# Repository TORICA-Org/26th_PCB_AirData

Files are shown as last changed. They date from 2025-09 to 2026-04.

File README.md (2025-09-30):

# 26th_PCB_AirData
メイン兼エアデータセンサー部（今後，エアデータと言います）のリポジトリです．
## 基板作成時の注意点
PCBエディターで基板上の配線をするときに気をつけてほしい点・できるだけ避けるべき点が書いてあります．これが全てではないのですが，最低限これらは守ってほしいです🙏( ｀・∀・´)ﾉﾖﾛｼｸ  
また，基板作成のコツを最後に載せてあります  
### KiCadの初期設定
これから表面実装化に向けた，小さく密度の高い基板を作ろうとするとKiCadの初期設定状態では不便が生じます．それは例えば配線のクリアランス（配線同士の最低間隔）やビア半径の初期設定値が大きすぎるためです．  
以下の画像下部のGNDビアはその上のコンデンサと同じぐらいの大きさになっていて，もはや邪魔です．  
  
そこで，以下の画像左上「ビア：ネットクラスのサイズを使用」からより小さい半径を指定できるのですが，[JLCPCBの製造能力](https://jlcpcb.com/jp/capabilities/pcb-capabilities)には限界があるわけでその限界を突破しないギリギリで設計する必要があります．その限界を突破していないか確認してくれる機能を活用するためにKiCad初期設定を変更します．この設定はプロジェクトを新たに作成する際に毎回設定する必要があります．  
  
ただし注意点の一つとして，**ビアのサイズを小さくすると急激に価格が跳ね上がる**ということがあります．これはJLCPCBの製造能力ページを見るだけではわからず，発注画面まで行って分かることなのですがビア外径0.4mm，内径0.3mmを下回るサイズのビアを打つとその個数に関わらず＋￥7200~9700されます．絶望ですね．はい...気をつけましょう．私はそんなことも知らず発注直前まで行って気付き，1430個のビアを打ち直すことになりました(┬┬﹏┬┬)
  
1. ファイル ＞ 基板の設定
  

2. デザインルール ＞ 制約


3. 以下のようにパラメータを変更  
  

---  

### USBの配線について
USBは差動伝送で通信しています．そのため，2本の配線のどちらかにだけノイズが乗ることや配線長に差があること，配線が長すぎることは避けるべきです．また，差動インピーダンスを考慮する必要があり，普段の配線よりも気を使う点が多いです．以下の点に気をつけて配線をお願いします．  
- 差動インピーダンスを90Ωに近づける（[JLCPCB公式計算ツール](https://jlcpcb.com/jp/pcb-impedance-calculator)）
- KiCad「配線 ＞ 差動ペアの配線」機能を使用する  
スクリーンショット (257)

- 同一レイヤー上で配線する（front面とback面を行き来しない）
- できるだけ配線を曲げず，一直線に配線する
- 電源線（5V，3.3Vなど）を近くに置かない
- Type-Cに接続するときに配線幅を変える必要がある場合，ティアドロップ（フィレット的な機能，以下「ティアドロップの使用」参照）を使用して滑らかに幅を変化させる  


- USB配線の裏面に別の配線を置かない（↓ダメな例）  
スクリーンショット 2025-09-01 164909

---

### テストポイント（TP）について
TPは基板を作ったあとに正しく信号が流れているかオシロスコープやテスターを用いて確認するために重要です．一方でノイズの発生源となったり逆にノイズを拾ったりすることも考えられます．その為，できるだけ少ない数配置すべきです．また，USBやGPIOなどの信号線にはできるだけ配置したくありません．どうしても配置する必要がある場合は，以下のように配線上に置くようにし，枝分かれしたところに置くことはやめてください．

---  

### ティアドロップの使用
今まで（25代まで）はパッドと配線の接続やビアとの接続時に特に何も考えずにやってきたと思います．ただ，これから密度の高い基板を作るにあたってノイズの発生を最大限に抑制する必要があり，急激な配線幅の変化をなくすべきです．今まで配線を90°に曲げるのは良くないと言われてきたのも同じ理由からです．そこでティアドロップ機能を使います．この機能は以下の画像の様に徐々に幅を変化させてくれるのでノイズが軽減されるはずです．また，この機能のオブジェクトはゾーンになっているため，機能が適応できない場合はゾーンが非表示になっていないか確認してください．以下がティアドロップの適用手順です．  
1.  編集 ＞ ティアドロップを編集  
  
2.  
3.   

--- 

### ビアについて
ビアには主に2つの目的があります．
- 配線をfrontからbackに移す（逆も然り）
- 層間のコンデンサ形成を防ぐ

例えば2層基板なら1層目と2層目の間の絶縁体を誘電体としたコンデンサにならないようにする．  
  
1つ目の目的でビアを使うのは一般的ですが，2つ目のコンデンサになるのを防ぐ目的でビアを使用しているか確認してください．置く位置はfrontとbackのベタGNDが重なっているところで，角になっている部分や近くにビアがないところです．定期的に配置することでコンデンサ化を防ぐ効果が高まります．  

---
### コンデンサを置く位置について  
コンデンサには電源や信号が不安定になった時にそれを補正してくれる役割があります．そのため，補正したい端子のできるだけ近くに置くことでその効果を十分に活用することができます．配線時にはそのコンデンサが

---
---
## 基板作成のコツ  
素子が多く，複雑な基板になればなるほど基板作成の難易度は上がります．どこに素子を置けば配線が最短になるのか，表と裏を無駄に行き来しないようにできるのか，見た目もきれいな基板になるのか，など考えることが増えていきます．そんな時に役に立つのが

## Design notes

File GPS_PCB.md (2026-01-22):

# GPS搭載基板の要求仕様書
~~ここでは実際に26代機(REWRITE)に載せるGPSを実装するための基板作成についての制約条件をまとめます．~~  
~~**来年27代機製作開発時に必要となるスキルを身に着けてもらいたいのであえて製作は27代メインで行ってもらうことにしました．**~~  
~~ただし，最初から最後まですべて丸投げするわけではないので安心してください．部室に来てくれればいつでも教えます!!　思い悩む前にどんどん来てね．~~  
終わりましたー！まさしありがとう

## 製作期限
＜kicad上での完成＞  
2025/12/31まで  
**期限厳守：別の作業に影響をきたします**  
  
## 要求仕様
### 基板概形
- 形状は長方形
- 幅21.1mm以下
- 長さはできるだけ小さく
- kicadの初期設定は[こちら](https://github.com/TORICA-Org/26th_PCB_AirData)を参照
- 配線幅は0.4mmとする
- ビアは直径0.45mm，スルーホール0.3mmとする
  
- 以下は別の基板だがこれとよく似た配置にしたい（片側にピンヘッダを半田付けできるようにし，外部とのやりとりはこのピンヘッダを介して行う）  


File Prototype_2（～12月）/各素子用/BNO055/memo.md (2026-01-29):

https://akizukidenshi.com/catalog/g/g116996/

U3 FXMA2102 これがライブラリにないかも　気にしなくていい．
テストポイント　

編集→ティアドロップ

ビア直径→JLCPCBの限界

文字の限界サイズ

2cm×1.5cm

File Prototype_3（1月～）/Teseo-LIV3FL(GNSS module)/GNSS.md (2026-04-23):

### Teseo-LIV3FL GNSS module
#### 部品

| 部品名 | 個数 | リンク | 備考 |
| --- | --- | --- | --- |
| IC1 Teseo-LIV3FLF | 1 | https://akizukidenshi.com/catalog/g/g130031/ |  |
| R1 200Ω | 1 |  https://www.sengoku.co.jp/mod/sgk_cart/detail.php?code=EEHD-0ECC# | SMD 3216 |
| R2 10Ω | 1 |  https://www.sengoku.co.jp/mod/sgk_cart/detail.php?code=EEHD-0EBH | SMD 3216 |
| C1 0.1μF | 1 | https://akizukidenshi.com/catalog/g/g116143/ | SMD 1608 |
| L1 27nH | 1 | https://www.monotaro.com/g/04259779/ | SMD 1005 サイズ小さい．表面実装できる？あと秋月にはない．|
| D1 LED | 1 | https://akizukidenshi.com/catalog/g/g109639/ | SMD 3216 |
| J1 コネクタ | 1 | https://akizukidenshi.com/catalog/g/g115417/ |  |
| アンテナ | 1 | https://akizukidenshi.com/catalog/g/g130030/ |  |

#### メモ
- 一応アクティブアンテナ向けに設計．回路的にはパッシブアンテナに切り替え可能．ただコネクタの形状が合わないかも．
- [このサイト](https://xsuz.github.io/blog/how_to_get_raw_data_from_teseo-liv3fl/)の回路とほぼ同じ
- 受信回路部分は同軸ケーブル経由でアクティブアンテナ（LNA内蔵）に電源を供給するため，Bias-Teeという回路を採用．[この動画（イチケン）](https://youtu.be/0PgLCQ8AsGs?si=6OudbEyScfQURzJA&t=123)でBias-Teeについて述べられている
- アンテナ周りに結構気を使ったつもり．受信する電波の周波数が1.57542GHzと高く，信号の反射などに気を付けなければならない（普通の回路だと配線長に対して信号の波長が十分に長く気にしなくていいが，配線長に対して信号の波長が短いと信号の反射や減衰などが生じて正しく電気信号が伝わらない．詳しくは「集中定数回路と分布定数回路」「RF回路」「高周波回路」などで検索）．この基板では信号の波長が約19cmなので一応気にしたほうがいい．
- アンテナの配線は特性インピーダンス50Ωで整合．KiCadの計算ツール使った．

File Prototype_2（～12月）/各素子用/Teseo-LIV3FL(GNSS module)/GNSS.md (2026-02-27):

### Teseo-LIV3FL GNSS module
#### 部品

| 部品名 | 個数 | リンク | 備考 | 店舗在庫情報 |
| --- | --- | --- | --- | --- |
| IC1 Teseo-LIV3FLF | 1 | https://akizukidenshi.com/catalog/g/g130031/ | | 秋月秋葉原店 2F 64番 |
| R1 200Ω | 1 | https://www.marutsu.co.jp/pc/i/240197/ | SMD 3216 | マルツ．ネットonly |
| R2 10Ω | 1 | https://www.marutsu.co.jp/pc/i/857080/ | SMD 3216 | マルツ，ネットonly |
| C1 0.1μF | 1 | https://akizukidenshi.com/catalog/g/g113374/ | SMD 1608 | 秋月秋葉原　1F 35番売場 5段目 |
| L1 27nH | 1 | https://www.monotaro.com/g/04259779/ | SMD 1005 サイズ小さい．表面実装できる？あと秋月にはない．| |
| D1 LED | 1 | →　半球型だからなぁ・・・変えたほうがいいかもな | SMD 3216 | https://akizukidenshi.com/catalog/g/g109639/ |
| J1 コネクタ | 1 | https://akizukidenshi.com/catalog/g/g115417/ |  | 秋月秋葉原店 2F 65番 |
| アンテナ | 1 | https://akizukidenshi.com/catalog/g/g130030/ | ←後継品が出てるっぽい |  |

#### メモ
- 一応アクティブアンテナ向けに設計．回路的にはパッシブアンテナに切り替え可能．ただコネクタの形状が合わないかも．
- [このサイト](https://xsuz.github.io/blog/how_to_get_raw_data_from_teseo-liv3fl/)の回路とほぼ同じ

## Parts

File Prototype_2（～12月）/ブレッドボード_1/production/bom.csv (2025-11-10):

Designator | Footprint | Quantity | Value | LCSC Part #
J1 | PinSocket_1x04_P2.54mm_Vertical | 1 | SDP31-500
J2 | PinSocket_1x06_P2.54mm_Vertical | 1 | AS5600_1
J3 | PinSocket_1x06_P2.54mm_Vertical | 1 | SD_1
J4 | PinSocket_1x06_P2.54mm_Vertical | 1 | AS5600_0
J5 | PinHeader_2x06_P2.54mm_Horizontal | 1 | Conn_01x12_Socket

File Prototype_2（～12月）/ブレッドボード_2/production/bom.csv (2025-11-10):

Designator | Footprint | Quantity | Value | LCSC Part #
J1, J6 | PinSocket_2x06_P2.54mm_Vertical | 2 | Conn_01x12_Socket
J2 | PinSocket_1x04_P2.54mm_Vertical | 1 | BMP390
J3 | PA_Connector_Post_2Pin | 1 | LiPo
U1, U2, U3, U4, U5 | Converter_DCDC_RECOM_R-78E-0.5_THT | 5 | MCP1703Ax-120xxDB
U6 | Seeeduino XIAO-MOUDLE14P-2.54-21X17.8MM | 1 | XIAO-ESP32-S3-SMD

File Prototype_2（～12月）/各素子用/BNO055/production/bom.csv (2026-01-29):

Designator | Footprint | Quantity | Value | LCSC Part #
C1 | 0805 | 1 | 10u
C10, C2, C3 | 0603 | 3 | 2.2u
C11, C9 | 0603 | 2 | 15p
C4, C5, C6, C7, C8 | 0402 | 5 | 100n
J2 | PinHeader_1x04_P2.54mm_Vertical | 1 | Conn_01x04_Socket
R1, R2, R4, R5 | 0603 | 4 | 10k
TP2, TP3, TP4, TP5 | TestPoint_Pad_1.0x1.0mm | 4 | TestPoint
U1 | SOT-23-5_HandSoldering | 1 | LP5907MFX-2.8
U2 | LGA-28_5.2x3.8mm_P0.5mm | 1 | BNO055
U3 | MICROPAK_FXMA2102L8X | 1 | ~
Y1 | Crystal_SMD_3215-2Pin_3.2x1.5mm | 1 | Crystal

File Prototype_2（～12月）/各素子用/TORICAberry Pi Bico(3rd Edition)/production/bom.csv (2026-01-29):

Designator | Footprint | Quantity | Value | LCSC Part #
C1, C10, C11, C12, C13, C2, C4, C6, C7, C8, C9 | 0201 | 11 | 100n
C14, C15 | 0201 | 2 | 15p
C16, C17, C18 | 0402 | 3 | 10u
C3, C5 | 0402 | 2 | 1u
D1, D2, D3, D4, D5, D6 | 0201 | 6 | LED
D7 | Schottly new SBR2U30P1 | 1 | D_Schottky
J1 | Type-C | 1 | USB_C_Receptacle
J2 | PinHeader_1x08_P2.54mm_Vertical | 1 | Conn_01x08_Socket
J3 | PinHeader_1x12_P2.54mm_Vertical | 1 | Conn_01x12_Socket
R1, R2 | 0402 | 2 | 27
R10, R5, R6, R7, R8, R9 | 0402 | 6 | 470
R11, R12 | 0402 | 2 | 5.1k
R3, R4 | 0402 | 2 | 1k
SW1, SW2 | Tactil Switch | 2 | SW_Push
U1 | QFN-56-1EP_7x7mm_P0.4mm_EP3.2x3.2mm | 1 | RP2040
U2 | Winbond_USON-8-1EP_3x2mm_P0.5mm_EP0.2x1.6mm | 1 | ~
U3 | 3pin regulator | 1 | NCP1117-3.3_TO252
Y1 | 12MHz | 1 | Crystal_GND24

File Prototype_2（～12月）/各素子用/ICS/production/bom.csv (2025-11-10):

Designator | Footprint | Quantity | Value | LCSC Part #
J1 | PinHeader_1x04_P2.54mm_Vertical | 1 | Conn_01x04_Socket
J2 | PinHeader_1x03_P2.54mm_Vertical | 1 | Conn_01x03_Socket
R1 | 0805 | 1 | 2.2k
U1 | 74AHC1G04W5 | 1 | ~
U2, U3 | 74AHC1G04W5 | 2 | 74AUC1G125

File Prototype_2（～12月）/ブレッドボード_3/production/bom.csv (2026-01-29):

Designator | Footprint | Quantity | Value | LCSC Part #
J1 | PinHeader_2x06_P2.54mm_Horizontal | 1 | Conn_01x12_Socket
J10 | CONN_B05B-PASK_JST | 1 | XIAO_Rudder
J11 | PA_Connector_Pos_4Pin | 1 | XIAO_Under
J12 | CONN_B02B-PASK-1_JST | 1 | SIG_ICS
J2 | PinSocket_1x04_P2.54mm_Vertical | 1 | BNO055
J3 | PinSocket_1x06_P2.54mm_Vertical | 1 | SD_0
J4 | PinSocket_1x04_P2.54mm_Vertical | 1 | GPS
J5 | PinHeader_1x12_P2.54mm_Vertical | 1 | Conn_01x12_Socket
J6 | PinSocket_1x04_P2.54mm_Vertical | 1 | ICS
J7 | PinSocket_1x08_P2.54mm_Vertical | 1 | Conn_01x08_Socket
J8 | PinSocket_1x03_P2.54mm_Vertical | 1 | ICS
J9 | PA_Connector_Post_2Pin | 1 | SPK

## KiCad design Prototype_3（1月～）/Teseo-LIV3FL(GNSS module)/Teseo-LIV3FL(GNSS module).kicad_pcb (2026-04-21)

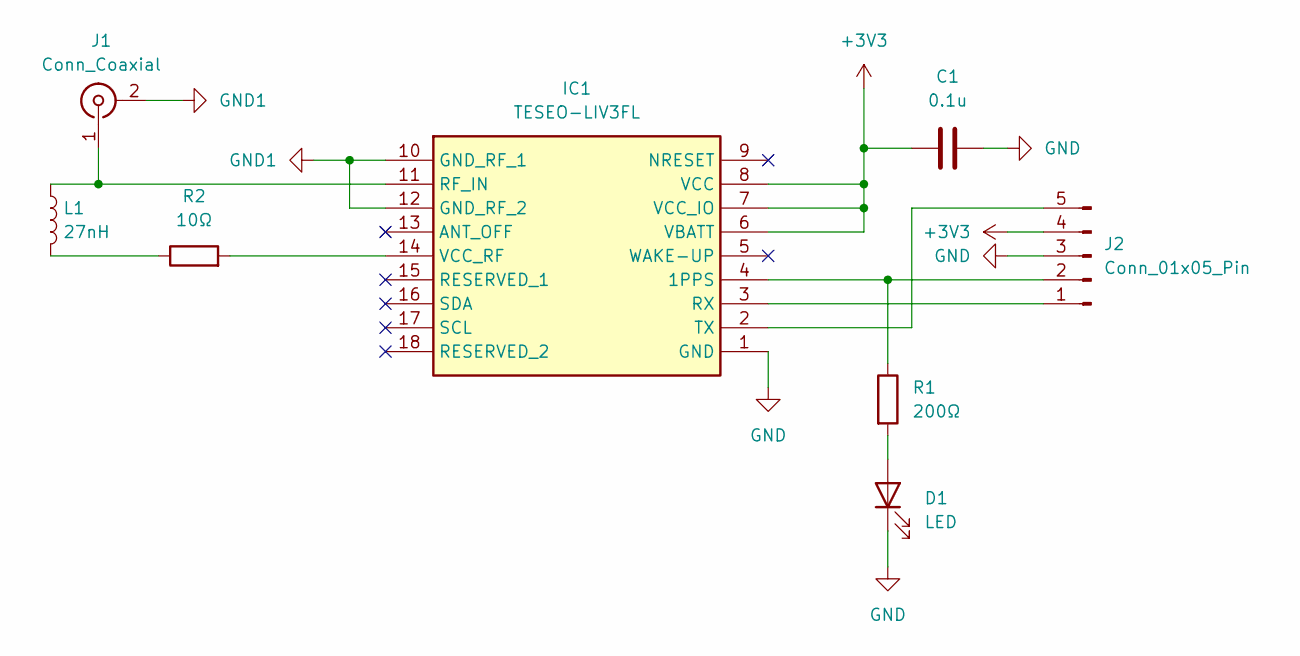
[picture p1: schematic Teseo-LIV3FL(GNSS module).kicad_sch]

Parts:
C1: 0.1u; C_0603_1608Metric_Pad1.08x0.95mm_HandSolder
D1: LED; LED_1206_3216Metric_Pad1.42x1.75mm_HandSolder
IC1: TESEO-LIV3FL; TESEOLIV3FL; Manufacturer_Part_Number TESEO-LIV3FL; Mouser Part Number 511-TESEO-LIV3FL
J1: Conn_Coaxial; U.FL_Hirose_U.FL-R-SMT-1_Vertical
J2: Conn_01x05_Pin; PinHeader_1x05_P2.54mm_Vertical
L1: 27nH; L_0402_1005Metric_Pad0.77x0.64mm_HandSolder
R1: 200Ω; C_1206_3216Metric_Pad1.33x1.80mm_HandSolder
R2: 10Ω; R_1206_3216Metric_Pad1.30x1.75mm_HandSolder

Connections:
+3V3: C1.1, IC1.6 (VBATT), IC1.7 (VCC_IO), IC1.8 (VCC), J2.4
GND: C1.2, D1.1 (K), IC1.1 (GND), J2.3
GND1: IC1.10 (GND_RF_1), IC1.12 (GND_RF_2), J1.2 (Ext)
unnamed: D1.2 (A), R1.2
unnamed: IC1.4 (1PPS), J2.2, R1.1
unnamed: IC1.11 (RF_IN), J1.1 (In), L1.1
unnamed: IC1.3 (RX), J2.1
unnamed: IC1.2 (TX), J2.5
unnamed: IC1.14 (VCC_RF), R2.2
unnamed: L1.2, R2.1

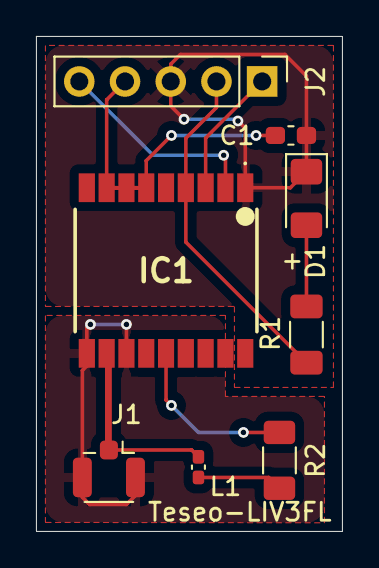
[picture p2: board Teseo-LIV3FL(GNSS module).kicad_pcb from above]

Board: 2 copper layers, 17.0 x 27.5 mm, 8 parts (0 on the bottom side), 10 nets.

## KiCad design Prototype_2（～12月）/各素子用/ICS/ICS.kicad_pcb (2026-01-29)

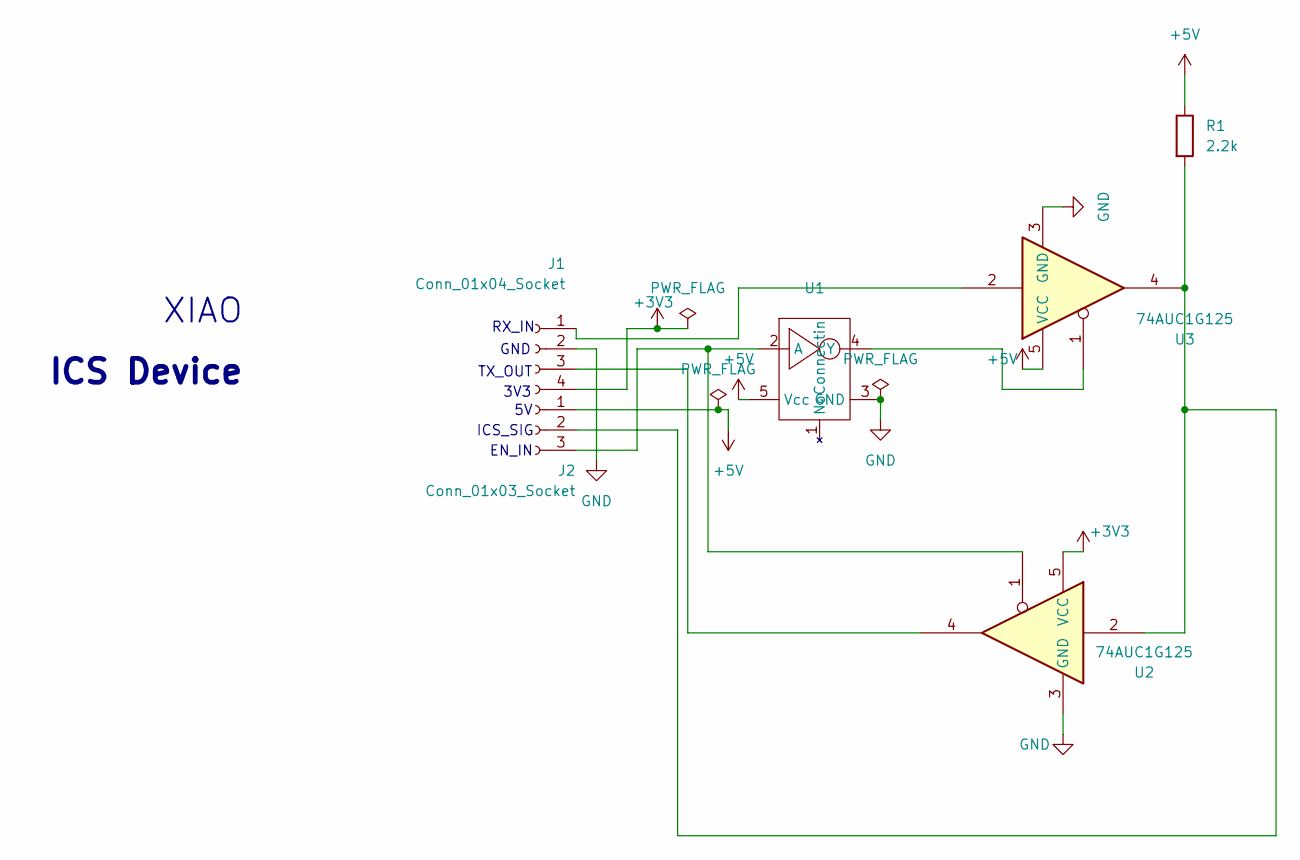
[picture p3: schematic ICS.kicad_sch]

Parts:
J1: Conn_01x04_Socket; PinHeader_1x04_P2.54mm_Vertical
J2: Conn_01x03_Socket; PinHeader_1x03_P2.54mm_Vertical
R1: 2.2k; R_0805_2012Metric
U1: 74AHC1G04W5
U2, U3: 74AUC1G125; 74AHC1G04W5

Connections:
+3V3: J1.4, U2.5 (VCC)
+5V: J2.1, R1.1, U1.5 (Vcc), U3.5 (VCC)
GND: J1.2, U1.3 (GND), U2.3 (GND), U3.3 (GND)
unnamed: J1.1, U3.2
unnamed: J1.3, U2.4
unnamed: J2.2, R1.2, U2.2, U3.4
unnamed: J2.3, U1.2 (A), U2.1
unnamed: U1.4 (Y), U3.1

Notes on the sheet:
TX_OUT
EN_IN
GND
RX_IN
ICS_SIG
ICS Device
3V3
XIAO

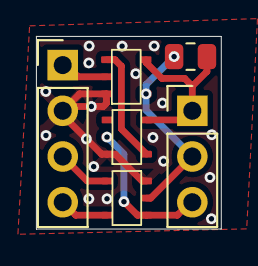
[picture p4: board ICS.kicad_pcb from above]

Board: 2 copper layers, 10.3 x 10.7 mm, 6 parts (0 on the bottom side), 8 nets.

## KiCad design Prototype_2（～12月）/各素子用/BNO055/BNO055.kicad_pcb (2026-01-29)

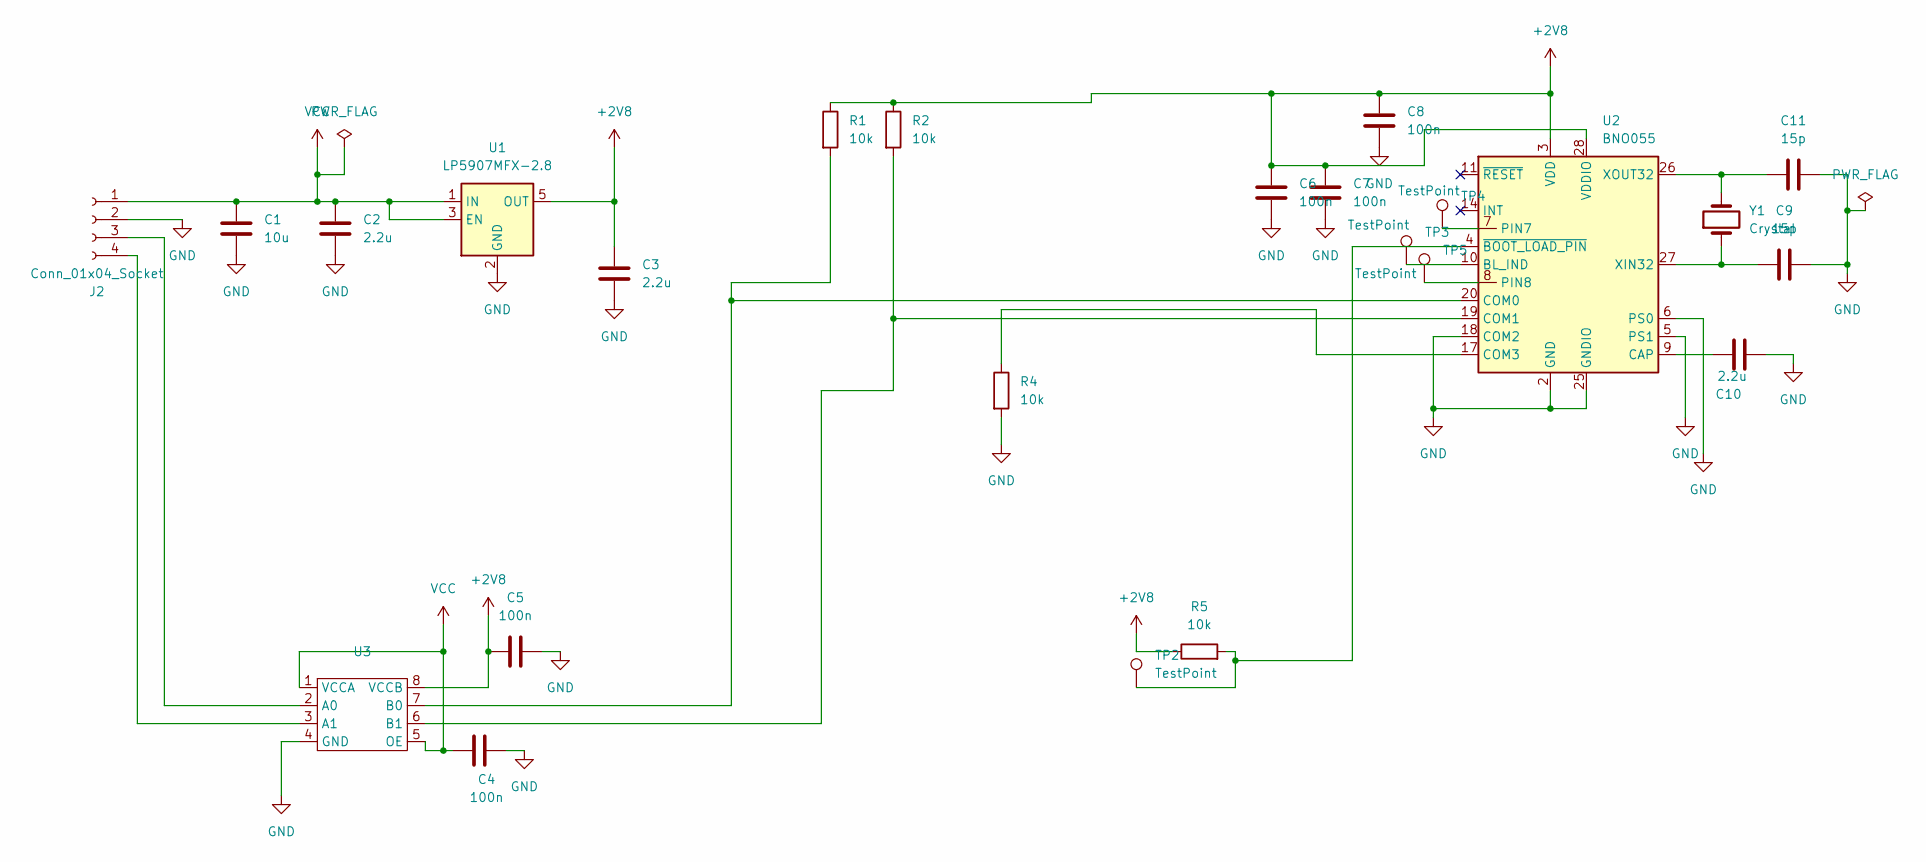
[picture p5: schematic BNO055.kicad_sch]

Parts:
C1: 10u; C_0805_2012Metric
C2, C3, C10: 2.2u; C_0603_1608Metric
C4, C5, C6, C7, C8: 100n; C_0402_1005Metric
C9, C11: 15p; C_0603_1608Metric
J2: Conn_01x04_Socket; PinHeader_1x04_P2.54mm_Vertical
R1, R2, R4, R5: 10k; R_0603_1608Metric
TP2, TP3, TP4, TP5: TestPoint; TestPoint_Pad_1.0x1.0mm
U1: LP5907MFX-2.8; SOT-23-5_HandSoldering
U2: BNO055; LGA-28_5.2x3.8mm_P0.5mm
U3: MICROPAK_FXMA2102L8X
Y1: Crystal; Crystal_SMD_3215-2Pin_3.2x1.5mm

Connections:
+2V8: C3.1, C5.1, C6.1, C7.1, C8.1, R1.1, R2.1, R5.1, U1.5 (OUT), U2.3 (VDD), U2.28 (VDDIO), U3.8 (VCCB)
GND: C1.2, C2.2, C3.2, C4.2, C5.2, C6.2, C7.2, C8.2, C9.2, C10.2, C11.2, J2.2, R4.2, U1.2 (GND), U2.2 (GND), U2.5 (PS1), U2.6 (PS0), U2.18 (COM2), U2.25 (GNDIO), U3.4 (GND)
unnamed: J2.3, U3.2 (A0)
unnamed: J2.4, U3.3 (A1)
unnamed: TP3.1, U2.10 (BL_IND)
unnamed: C10.1, U2.9 (CAP)
unnamed: R1.2, U2.20 (COM0), U3.7 (B0)
unnamed: R2.2, U2.19 (COM1), U3.6 (B1)
unnamed: R4.1, U2.17 (COM3)
unnamed: TP4.1, U2.7 (PIN7)
unnamed: TP5.1, U2.8 (PIN8)
unnamed: C9.1, U2.27 (XIN32), Y1.1
unnamed: C11.1, U2.26 (XOUT32), Y1.2
unnamed: R5.2, TP2.1, U2.4 (~BOOT_LOAD_PIN)
VCC: C1.1, C2.1, C4.1, J2.1, U1.1 (IN), U1.3 (EN), U3.1 (VCCA), U3.5 (OE)

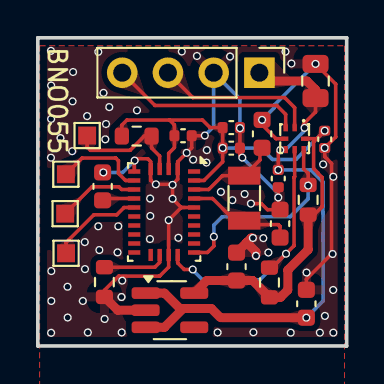
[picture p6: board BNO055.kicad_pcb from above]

Board: 2 copper layers, 17.2 x 17.1 mm, 24 parts (0 on the bottom side), 15 nets.

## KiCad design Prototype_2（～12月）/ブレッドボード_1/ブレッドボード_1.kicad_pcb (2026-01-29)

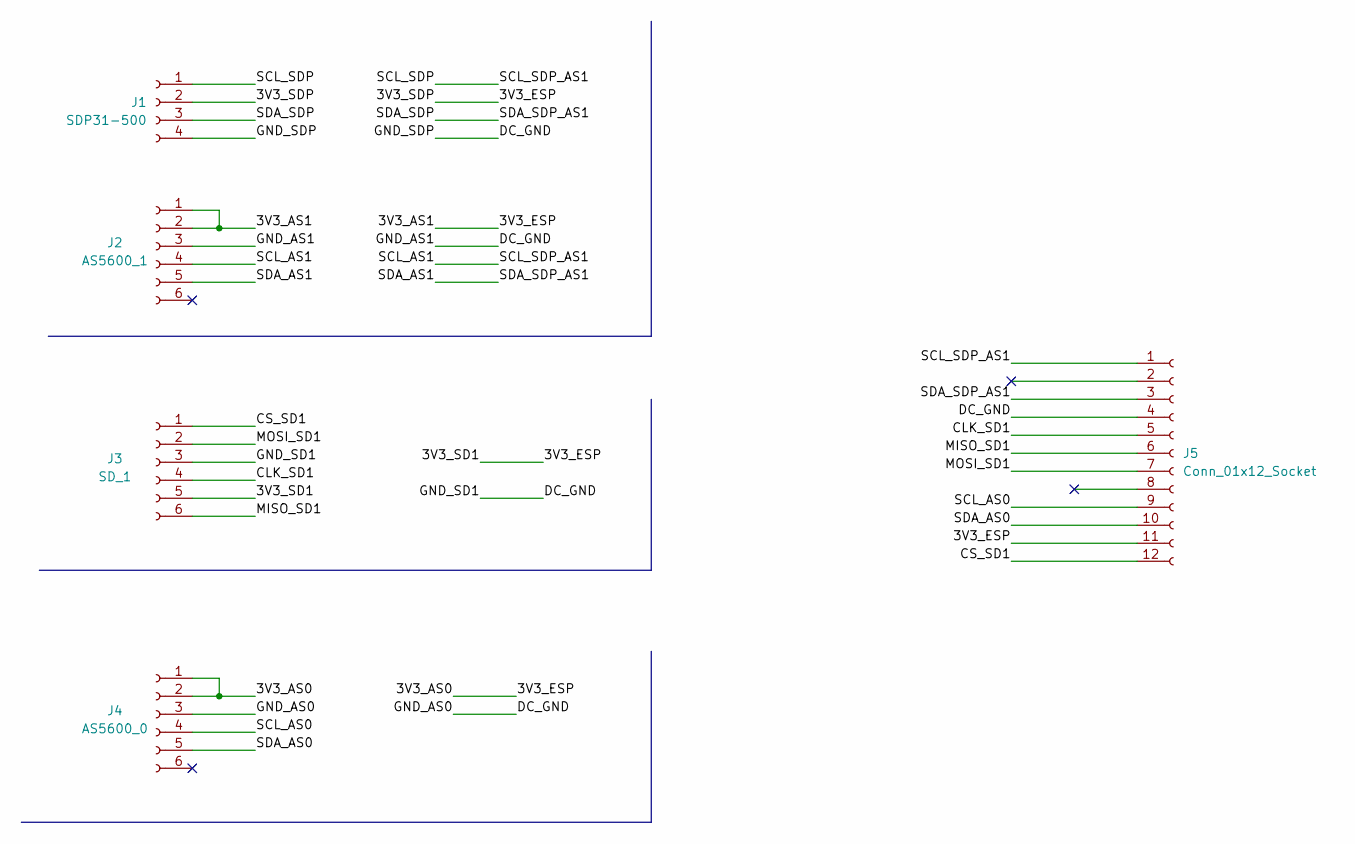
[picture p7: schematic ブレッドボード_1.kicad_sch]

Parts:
J1: SDP31-500; PinSocket_1x04_P2.54mm_Vertical
J2: AS5600_1; PinSocket_1x06_P2.54mm_Vertical
J3: SD_1; PinSocket_1x06_P2.54mm_Vertical
J4: AS5600_0; PinSocket_1x06_P2.54mm_Vertical
J5: Conn_01x12_Socket; PinHeader_2x06_P2.54mm_Horizontal

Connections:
/3V3_AS0: J1.2, J2.1, J2.2, J3.5, J4.1, J4.2, J5.11
/CLK_SD1: J3.4, J5.5
/CS_SD1: J3.1, J5.12
/DC_GND: J1.4, J2.3, J3.3, J4.3, J5.4
/MISO_SD1: J3.6, J5.6
/MOSI_SD1: J3.2, J5.7
/SCL_AS0: J4.4, J5.9
/SCL_AS1: J1.1, J2.4, J5.1
/SDA_AS0: J4.5, J5.10
/SDA_AS1: J1.3, J2.5, J5.3

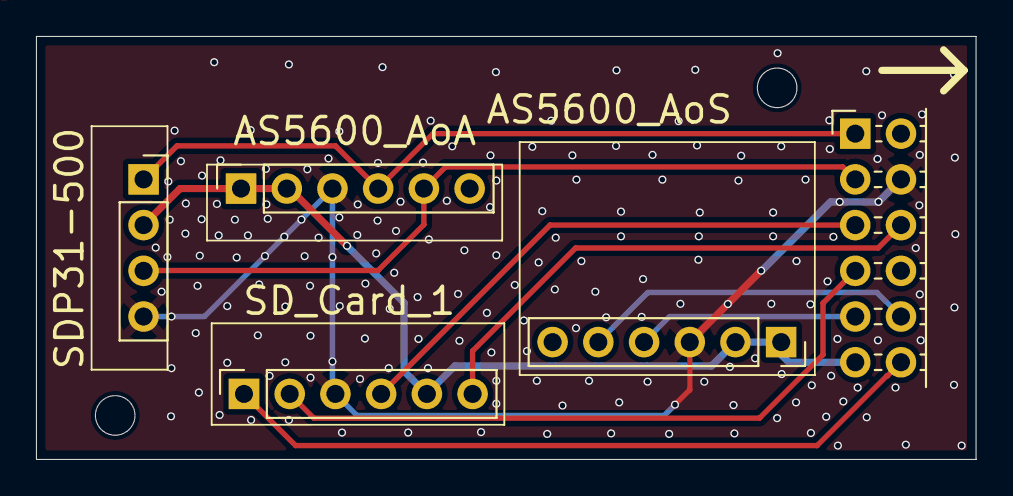
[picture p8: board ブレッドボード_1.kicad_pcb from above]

Board: 2 copper layers, 52.2 x 23.5 mm, 5 parts (0 on the bottom side), 10 nets.

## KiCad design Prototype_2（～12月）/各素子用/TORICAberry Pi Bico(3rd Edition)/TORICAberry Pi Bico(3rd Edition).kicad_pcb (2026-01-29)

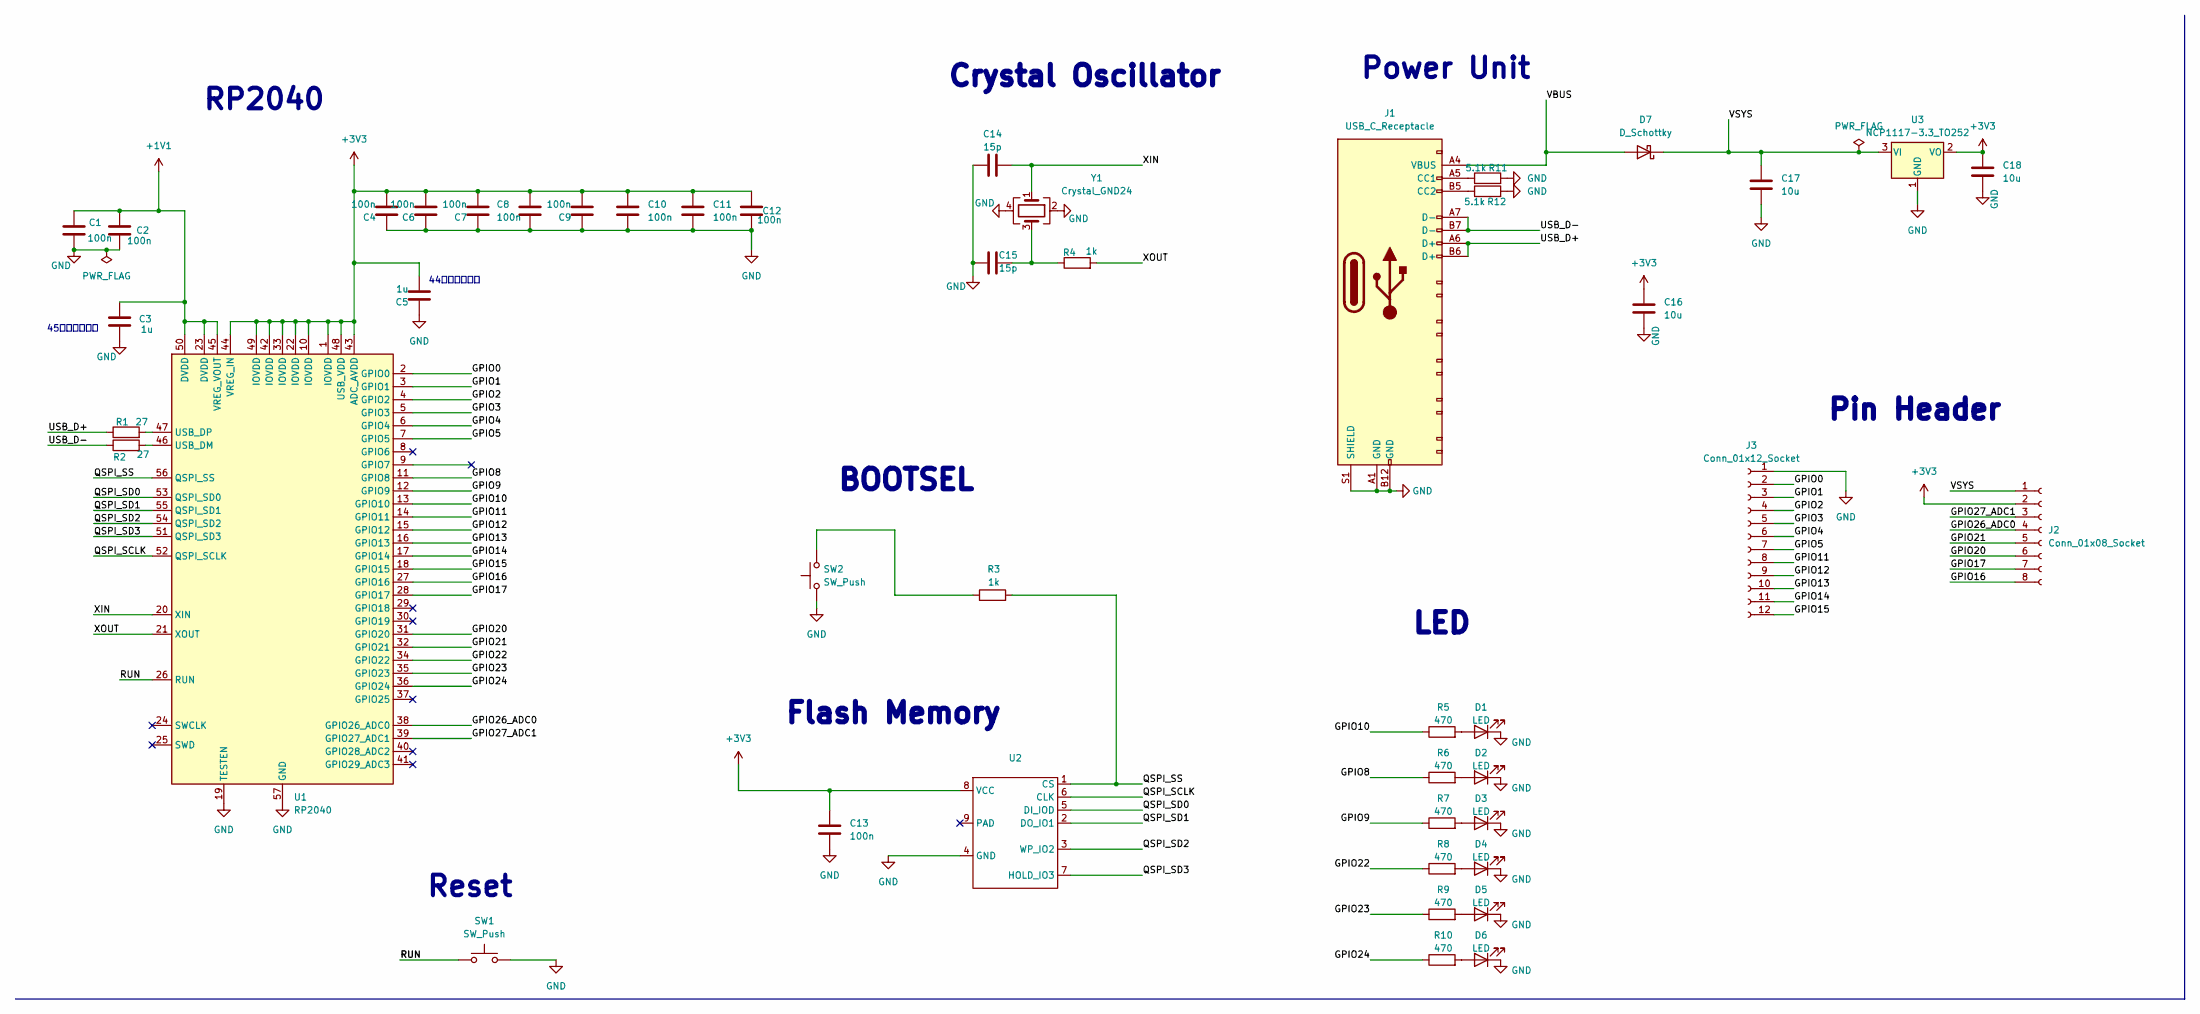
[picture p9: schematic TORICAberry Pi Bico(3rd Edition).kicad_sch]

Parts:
C1, C2, C4, C6, C7, C8, C9, C10, C11, C12, C13: 100n; C_0201_0603Metric
C3, C5: 1u; C_0402_1005Metric
C14, C15: 15p; C_0201_0603Metric
C16, C17, C18: 10u; C_0402_1005Metric
D1, D2, D3, D4, D5, D6: LED; LED_0201_0603Metric
D7: D_Schottky; Schottly new SBR2U30P1
J1: USB_C_Receptacle; Type-C
J2: Conn_01x08_Socket; PinHeader_1x08_P2.54mm_Vertical
J3: Conn_01x12_Socket; PinHeader_1x12_P2.54mm_Vertical
R1, R2: 27; R_0402_1005Metric
R3, R4: 1k; R_0402_1005Metric
R5, R6, R7, R8, R9, R10: 470; R_0402_1005Metric
R11, R12: 5.1k; R_0402_1005Metric
SW1, SW2: SW_Push; Tactil Switch
U1: RP2040; QFN-56-1EP_7x7mm_P0.4mm_EP3.2x3.2mm
U2: Winbond_USON-8-1EP_3x2mm_P0.5mm_EP0.2x1.6mm
U3: NCP1117-3.3_TO252; 3pin regulator
Y1: Crystal_GND24; 12MHz

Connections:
+1V1: C1.2, C2.2, C3.2, U1.23 (DVDD), U1.45 (VREG_VOUT), U1.50 (DVDD)
+3V3: C4.2, C5.2, C6.2, C7.2, C8.2, C9.2, C10.1, C11.1, C12.2, C13.1, C16.1, C18.1, J2.2, U1.1 (IOVDD), U1.10 (IOVDD), U1.22 (IOVDD), U1.33 (IOVDD), U1.42 (IOVDD), U1.43 (ADC_AVDD), U1.44 (VREG_IN), U1.48 (USB_VDD), U1.49 (IOVDD), U2.8 (VCC), U3.2 (VO)
/GPIO0: J3.2, U1.2 (GPIO0)
/GPIO1: J3.3, U1.3 (GPIO1)
/GPIO2: J3.4, U1.4 (GPIO2)
/GPIO3: J3.5, U1.5 (GPIO3)
/GPIO4: J3.6, U1.6 (GPIO4)
/GPIO5: J3.7, U1.7 (GPIO5)
/GPIO8: R6.1, U1.11 (GPIO8)
/GPIO9: R7.1, U1.12 (GPIO9)
/GPIO10: R5.1, U1.13 (GPIO10)
/GPIO11: J3.8, U1.14 (GPIO11)
/GPIO12: J3.9, U1.15 (GPIO12)
/GPIO13: J3.10, U1.16 (GPIO13)
/GPIO14: J3.11, U1.17 (GPIO14)
/GPIO15: J3.12, U1.18 (GPIO15)
/GPIO16: J2.8, U1.27 (GPIO16)
/GPIO17: J2.7, U1.28 (GPIO17)
/GPIO20: J2.6, U1.31 (GPIO20)
/GPIO21: J2.5, U1.32 (GPIO21)
/GPIO22: R8.1, U1.34 (GPIO22)
/GPIO23: R9.1, U1.35 (GPIO23)
/GPIO24: R10.1, U1.36 (GPIO24)
/GPIO26_ADC0: J2.4, U1.38 (GPIO26_ADC0)
/GPIO27_ADC1: J2.3, U1.39 (GPIO27_ADC1)
/QSPI_SCLK: U1.52 (QSPI_SCLK), U2.6 (CLK)
/QSPI_SD0: U1.53 (QSPI_SD0), U2.5 (DI_IOD)
/QSPI_SD1: U1.55 (QSPI_SD1), U2.2 (DO_IO1)
/QSPI_SD2: U1.54 (QSPI_SD2), U2.3 (WP_IO2)
/QSPI_SD3: U1.51 (QSPI_SD3), U2.7 (HOLD_IO3)
/QSPI_SS: R3.2, U1.56 (QSPI_SS), U2.1 (CS)
/RUN: SW1.1, U1.26 (RUN)
/USB_D+: J1.A6 (D+), J1.B6 (D+), R1.1
/USB_D-: J1.A7 (D-), J1.B7 (D-), R2.1
/VBUS: D7.2 (A), J1.A4 (VBUS)
/VSYS: C17.1, D7.1 (K), J2.1, U3.3 (VI)
/XIN: C14.2, U1.20 (XIN), Y1.1
/XOUT: R4.2, U1.21 (XOUT)
GND: C1.1, C2.1, C3.1, C4.1, C5.1, C6.1, C7.1, C8.1, C9.1, C10.2, C11.2, C12.1, C13.2, C14.1, C15.1, C16.2, C17.2, C18.2, D1.1 (K), D2.1 (K), D3.1 (K), D4.1 (K), D5.1 (K), D6.1 (K), J1.A1 (GND), J1.B12 (GND), J1.S1 (SHIELD), J3.1, R11.2, R12.2, SW1.2, SW2.1, U1.19 (TESTEN), U1.57 (GND), U2.4 (GND), U3.1 (GND), Y1.2, Y1.4
unnamed: C15.2, R4.1, Y1.3
unnamed: D1.2 (A), R5.2
unnamed: D2.2 (A), R6.2
unnamed: D3.2 (A), R7.2
unnamed: D4.2 (A), R8.2
unnamed: D5.2 (A), R9.2
unnamed: D6.2 (A), R10.2
unnamed: J1.A5 (CC1), R11.1
unnamed: J1.B5 (CC2), R12.1
unnamed: R3.1, SW2.2
unnamed: R2.2, U1.46 (USB_DM)
unnamed: R1.2, U1.47 (USB_DP)

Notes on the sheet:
44の近くに配置
Reset
Flash Memory
RP2040
Power Unit
Pin Header
45の近くに配置
BOOTSEL
Crystal Oscillator
LED

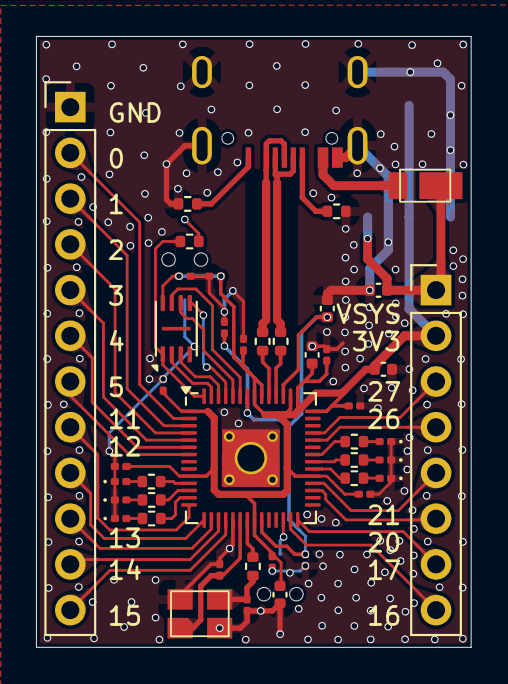
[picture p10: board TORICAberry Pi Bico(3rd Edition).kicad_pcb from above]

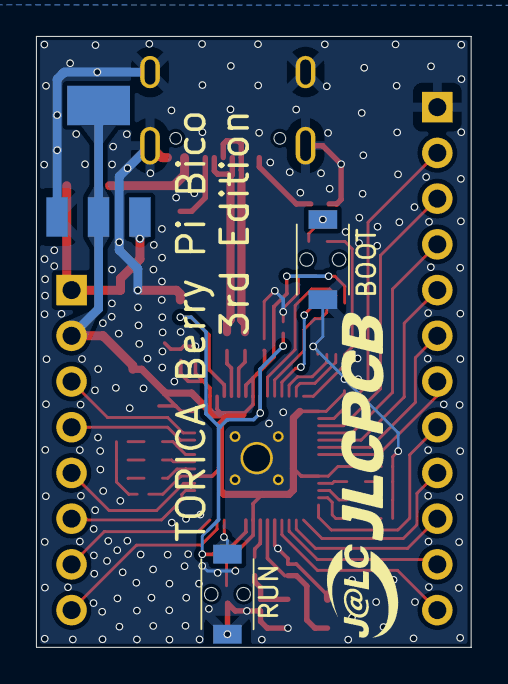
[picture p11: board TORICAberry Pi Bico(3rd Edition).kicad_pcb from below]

Board: 2 copper layers, 24.2 x 33.9 mm, 46 parts (3 on the bottom side), 51 nets.

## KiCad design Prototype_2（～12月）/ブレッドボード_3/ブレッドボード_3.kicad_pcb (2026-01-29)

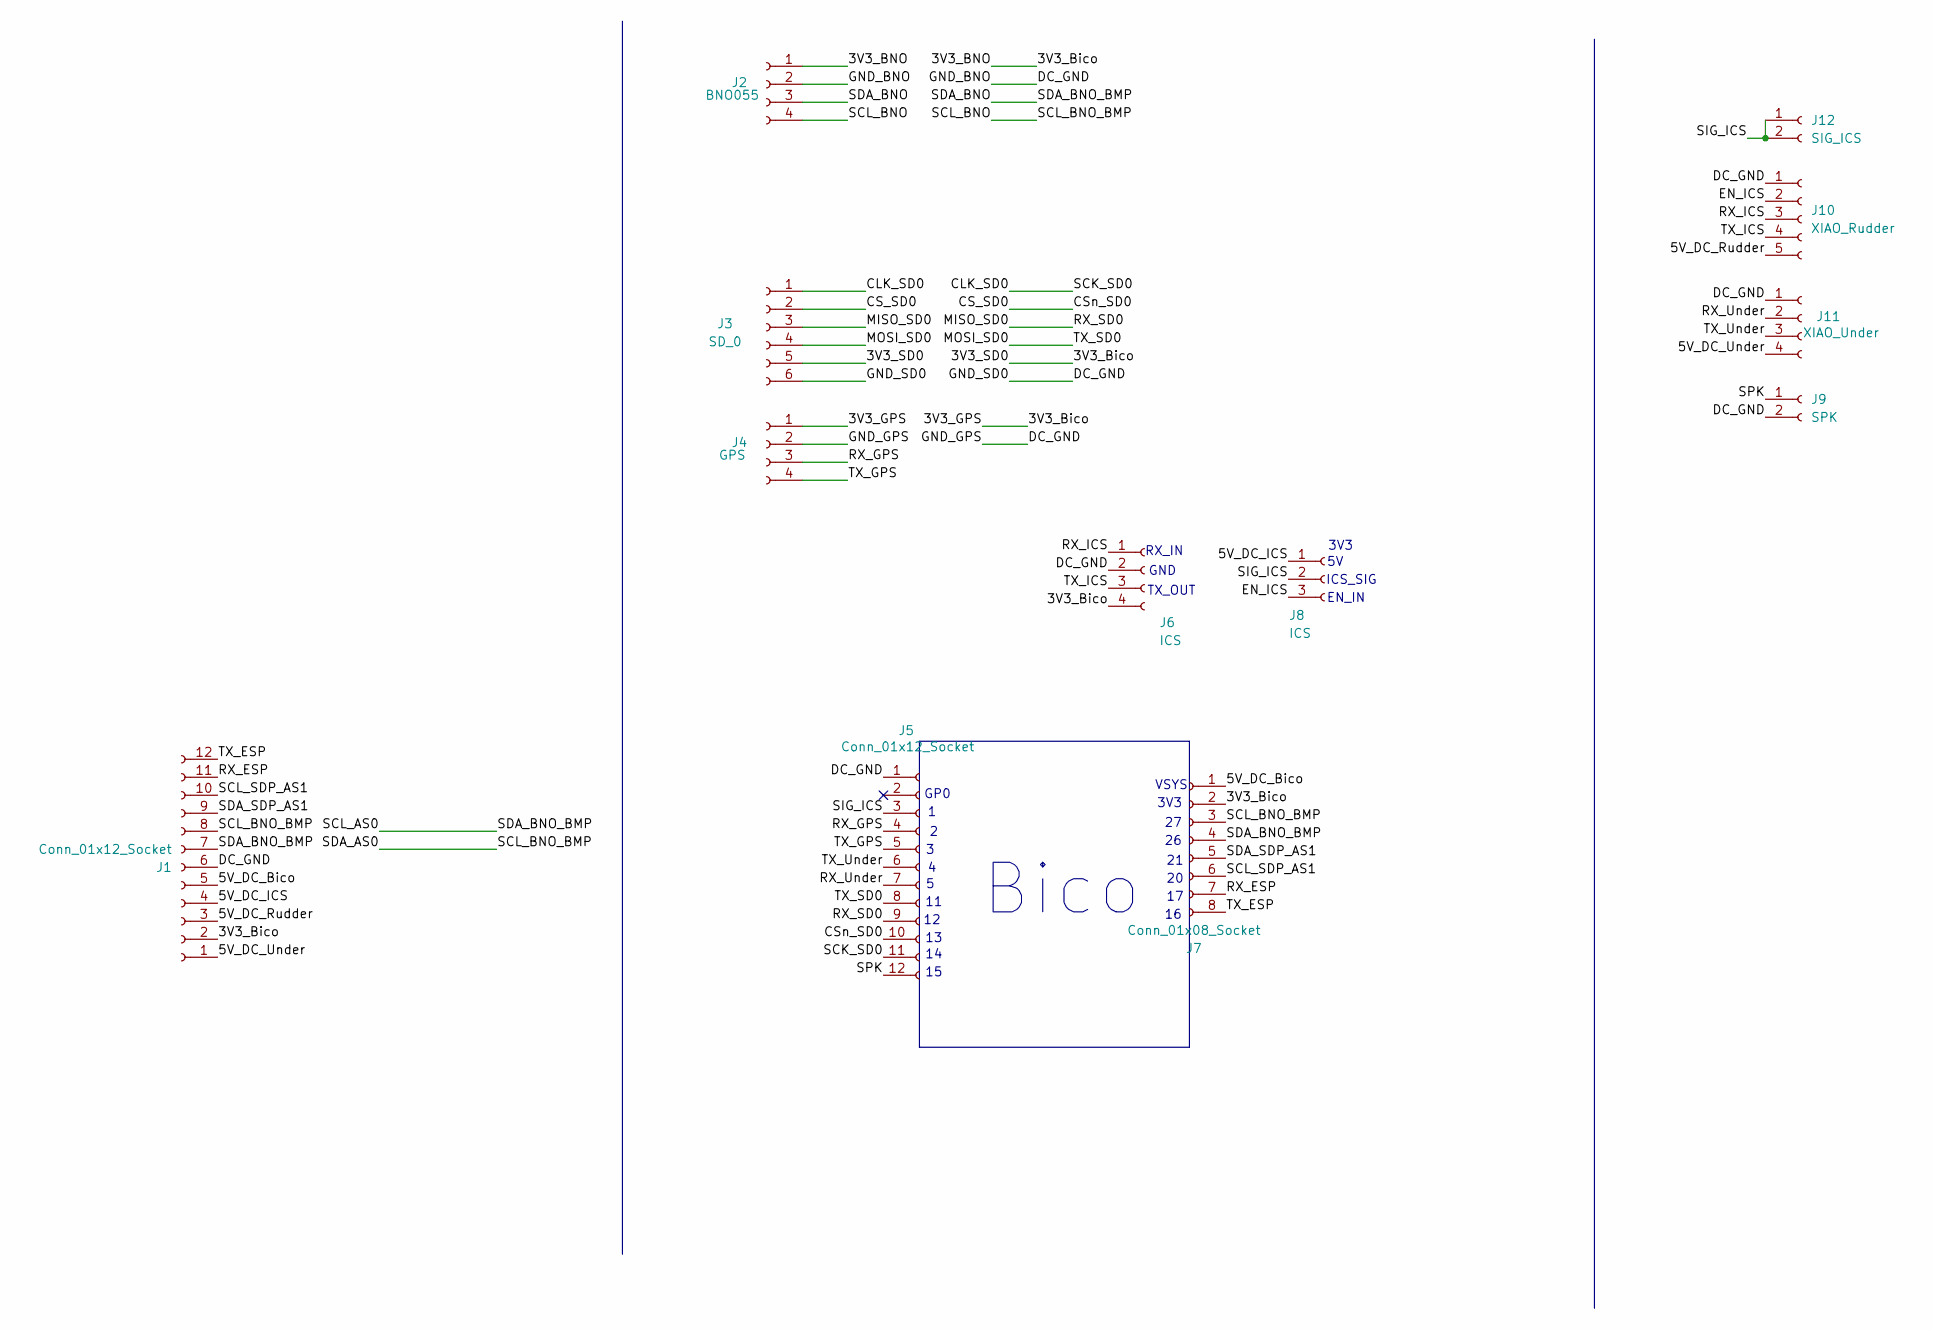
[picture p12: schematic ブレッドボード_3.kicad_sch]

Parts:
J1: Conn_01x12_Socket; PinHeader_2x06_P2.54mm_Horizontal
J2: BNO055; PinSocket_1x04_P2.54mm_Vertical
J3: SD_0; PinSocket_1x06_P2.54mm_Vertical
J4: GPS; PinSocket_1x04_P2.54mm_Vertical
J5: Conn_01x12_Socket; PinHeader_1x12_P2.54mm_Vertical
J6: ICS; PinSocket_1x04_P2.54mm_Vertical
J7: Conn_01x08_Socket; PinSocket_1x08_P2.54mm_Vertical
J8: ICS; PinSocket_1x03_P2.54mm_Vertical
J9: SPK; PA_Connector_Post_2Pin
J10: XIAO_Rudder; CONN_B05B-PASK_JST
J11: XIAO_Under; PA_Connector_Pos_4Pin
J12: SIG_ICS; CONN_B02B-PASK-1_JST

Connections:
/3V3_BNO: J1.2, J2.1, J3.5, J4.1, J6.4, J7.2
/5V_DC_Bico: J1.5, J7.1
/5V_DC_ICS: J1.4, J8.1
/5V_DC_Rudder: J1.3, J10.5
/5V_DC_Under: J1.1, J11.4
/CLK_SD0: J3.1, J5.11
/CS_SD0: J3.2, J5.10
/DC_GND: J1.6, J2.2, J3.6, J4.2, J5.1, J6.2, J9.2, J10.1, J11.1
/EN_ICS: J8.3, J10.2
/MISO_SD0: J3.3, J5.9
/MOSI_SD0: J3.4, J5.8
/RX_ESP: J1.11, J7.7
/RX_GPS: J4.3, J5.4
/RX_ICS: J6.1, J10.3
/RX_Under: J5.7, J11.2
/SCL_AS0: J1.7, J2.3, J7.4
/SCL_BNO: J1.8, J2.4, J7.3
/SCL_SDP_AS1: J1.10, J7.6
/SDA_SDP_AS1: J1.9, J7.5
/SIG_ICS: J5.3, J8.2, J12.1, J12.2
/SPK: J5.12, J9.1
/TX_ESP: J1.12, J7.8
/TX_GPS: J4.4, J5.5
/TX_ICS: J6.3, J10.4
/TX_Under: J5.6, J11.3

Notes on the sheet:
GP0
3V3
TX_OUT
EN_IN
GND
VSYS
RX_IN
Bico
ICS_SIG



Board: 2 copper layers, 100.0 x 23.5 mm, 12 parts (4 on the bottom side), 25 nets.

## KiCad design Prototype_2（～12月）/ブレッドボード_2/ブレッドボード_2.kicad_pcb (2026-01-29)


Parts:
J1, J6: Conn_01x12_Socket; PinSocket_2x06_P2.54mm_Vertical
J2: BMP390; PinSocket_1x04_P2.54mm_Vertical
J3: LiPo; PA_Connector_Post_2Pin
U1, U2, U3, U4, U5: MCP1703Ax-120xxDB; Converter_DCDC_RECOM_R-78E-0.5_THT
U6: XIAO-ESP32-S3-SMD; Seeeduino XIAO-MOUDLE14P-2.54-21X17.8MM

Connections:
/3V3_BMP: J2.1, J6.11
/3V3_ESP: J1.11, U6.12 (3V3)
/5V_DC_Bico: J6.8, U2.3 (VO)
/5V_DC_ESP: U3.3 (VO), U6.14 (5V)
/5V_DC_ICS: J6.9, U1.3 (VO)
/5V_DC_Rudder: J6.10, U4.3 (VO)
/5V_DC_Under: J6.12, U5.3 (VO)
/CLK_SD1: J1.5, U6.9 (GPIO7_A8_D8_SCK)
/CS_SD1: J1.12, U6.1 (GPIO1_A0_D0)
/DC_GND: J1.4, J2.2, J3.2, J6.7, U1.2 (GND), U2.2 (GND), U3.2 (GND), U4.2 (GND), U5.2 (GND), U6.13 (GND)
/LiPo: J3.1, U1.1 (VI), U2.1 (VI), U3.1 (VI), U4.1 (VI), U5.1 (VI)
/MISO_SD1: J1.6, U6.10 (GPIO8_A9_D9_MISO)
/MOSI_SD1: J1.7, U6.11 (GPIO9_A10_D10_MOSI)
/RX_ESP: J6.2, U6.8 (GPIO44_D7_RX)
/SCK_BMP: J1.9, J2.3, J6.5
/SCL_SDP_AS1: J1.1, J6.3
/SDA_AS0: J1.10, J2.4, J6.6
/SDA_SDP_AS1: J1.3, J6.4
/TX_ESP: J6.1, U6.7 (GPIO43_A6_D6_TX)

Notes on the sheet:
Under
ICS
ESP32
Rudder
Bico


Board: 2 copper layers, 100.0 x 23.5 mm, 10 parts (1 on the bottom side), 19 nets.

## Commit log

2025-08-31 注意点書き始めた
2025-08-31 README.md の更新
2025-11-06 理大祭 兼 部品展示会 兼 試作用基板
    各素子用.zipに"BNO055"，"ICS"，"Bico"が入ってます．
    ブレッドボード.zipに"ブレッドボード1"，"ブレッドボード2"，"ブレッドボード3"が入ってます．
    全部まとめると25MB以上になっちゃってアップロードできなかったからしょうがなく分割しました．
2025-11-06 ネジ追加
2025-11-06 コネクタの位置変えた
2025-11-07 RX-ESP delete
    [BNO055.kicad_pcb, BNO055.kicad_sch, TORICAberry Pi Bico(3rd Edition).kicad_pcb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]
2025-11-07 change Conn 5P to 6P
    [bom.csv, positions.csv, ブレッドボード_3.kicad_pcb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]
2025-11-10 家のPCで更新
    [BNO055.kicad_pcb, ICS.kicad_pcb, TORICAberry Pi Bico(3rd Edition).kicad_pcb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]
2025-12-31 Create GPS_PCB
    [Teseo-LIV3FL(GNSS module).kicad_pcb, Teseo-LIV3FL(GNSS module).kicad_sch]
2025-12-31 Change board width
    [Teseo-LIV3FL(GNSS module).kicad_pcb]
2026-01-22 Create Prototype_2
2026-01-22 まだ前回から変更できてないところあるけどとりあえず
2026-01-22 前回からまだ未変更有り
2026-01-29 For Atsuki
    [BNO055.dsn, BNO055.kicad_pcb, BNO055.kicad_sch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]
2026-04-07 modified Teseo GNSS
    [Teseo-LIV3FL(GNSS module)-B_Cu.gbr, Teseo-LIV3FL(GNSS module)-B_Mask.gbr, Teseo-LIV3FL(GNSS module)-B_Paste.gbr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]
2026-04-20 GNSS.md の更新
2026-04-21 Teseo
    シルク印刷修正
    - ピン名
    シルク印刷追加
    - LED Anode端子
    - IC1 pin1丸印
    [Teseo-LIV3FL(GNSS module)-B_Cu.gbr, Teseo-LIV3FL(GNSS module)-B_Mask.gbr, Teseo-LIV3FL(GNSS module)-B_Paste.gbr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]
2026-04-23 GNSS設計メモ追加
2026-05-23 ブレボ以外は完成，ブレボは残りAS位置調整
